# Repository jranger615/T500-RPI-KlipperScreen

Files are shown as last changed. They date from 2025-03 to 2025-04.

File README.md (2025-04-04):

 # T500-RPI-KlipperScreen
Tired of the TouchPad for the t500, here we will build our own
This Klipper screen should work for other klipper machines but may require other conifguration changes and a new mount

mail google

> [!IMPORTANT]
>### RPI5 Version
> * Added RPI5 version of STLs.
> * It however may require different usb/pwr wires/buck converter.
> * Uses official RPI5 FAN

> ### If you wish to tip and help continue my work on mods please use:
>* Paypal: Jeff.b.ranger@gmail.com
>* Venmo: @Jeff-Ranger-1

## Things to BUY
  * Raspberry PI 4B 4GB RAM https://chicagodist.com/products/raspberry-pi-4-model-b-4gb  (I will remodel this for RPi5 as well)
  * SD Card https://chicagodist.com/products/raspberry-pi-official-noobs-microsd-card?variant=40342062268495
  * SD Card Reader (If your Laptop or COmputer Doesnt Have one)
  * 7" Touch Screen https://www.amazon.com/dp/B0B2QW89DR?ref_=ppx_hzsearch_conn_dt_b_fed_asin_title_2
  * 24v > 5V BUCK Power Adapter https://www.amazon.com/dp/B0CRVW7N2J 
  * HDMI Cord https://www.amazon.com/dp/B0CCKXH13W
  * USBA-USBC Cord https://www.amazon.com/dp/B0BRQY1FLG
  * USBA-USB Micro Cord https://www.amazon.com/dp/B0BHNVLW1Z
  * USB-C Extension https://www.amazon.com/dp/B0DKHPS1L3
  * M3 and M4 Heat Inserts
  * **Optional**  Power Supply https://www.amazon.com/dp/B0BMGJNSVS (This just makes it easier to power your Pi and do your configurations not attached to your printer)
  * m3 bolts
  * m4x6 bolts (Attatchment to Printer)
  * Screws https://www.amazon.com/dp/B078ZVQ7XM (Mounts the LCD Screen to case)
  * RPI4 Fan https://www.amazon.com/dp/B091L1XKL6

## Software to Download
  * Raspberry Pi Imager https://www.raspberrypi.com/software/
  * Putty https://www.chiark.greenend.org.uk/~sgtatham/putty/latest.html

## Things to Print
Located: https://github.com/jranger615/T500-RPI-KlipperScreen/tree/main/stl
  * LCD_FRONT.stl
  * RPI4_LCD_BACK.stl
  * RPI4-TOP.stl
  * Vertical-LCD-Mount.stl or Horizon-LCD-Mount.stl
    
 

## Install Mainsail on SD CARD
  * First, take the MicroSD you’ll use for your Raspberry Pi and connect it to your computer. 
  * $Download and install the Pi Imager tool and launch it.
  * Click Choose Device, and select Raspberry PI 4
  * Click “Choose OS”, scroll down to “Other specific-purpose OS”, choose “3D printing”, and then select Mainsail OS.
  * Choose Storage, and make sure to select the SD card.
  * Click Next
  * Click Edit Setting
    
    
  * Set a Host name of your choice
  * set MKS as the user  (***This is important so we dont have to edit many configs on the t500)
    
    
  * Set makerbase as the password
  * Enable and SET your WIFI Settings
  * Click Save
  * Click Yes
  * Click Yes to write to SD Card
  * Once Complete put the SD Card in your Raspberry PI

## Install Kiauh
 * Attach your Raspberry PI to the power cord and turn it on
 * Open Putty.exe and add host name you used in the Mainsial install  EX: mkspiB.local  (May need to attach network cord if wifi doesnt work after a couple minutes)
   
 
 * Click Open
 * Click Accept
  
  

 * Enter user: MKS 
 * Click enter
 * Enter password: makerbase
 * Click Enter
 * Type: sudo apt-get update && sudo apt-get install git -y
 * click enter
 * Enter password: makerbase
 * Click enter
 * type: cd ~ && git clone https://github.com/dw-0/kiauh.git
 * click enter
 * type: ./kiauh/kiauh.sh
 * click enter
 
 
 * type: 1 and click enter
 * type: 1 and click enter to install
 * type 7 and click enter
   
  

 * When Prompted "Press enter for default (Yes) [Y/n]" Click Enter
 * When Prompted "Press enter for default (Xserver) Backend Xserver or Wayland (cage)? x/w" Click Enter  (This will take awhile to complete)
 * When Prompted "Install NetworkMangher for the network panel [Y/n]" Type Y
 * Click enter

 ## Install Kamp 
  If you are not currently using KAMP you can skip this step 

 * Reconnect to putty like above
 * Browse to https://github.com/kyleisah/Klipper-Adaptive-Meshing-Purging and follow the installation commands

## Fix Wifi Configurations (This is only needed if all WIFI options arent showing up)
When you first set up a Raspberry Pi, sometimes you'll need to manually set the timezone/location to allow you to make a WiFi connection (even though the initial setup screens appear to set this for you). 
* Putty into your device
* type: sudo raspi-config
  
 
* Select Localization Options again and Selec WLAN Country
* Set TimeZone
* Select Localization Options again and Selec WLAN Country
* Press the Right Direction button and Click Finish
* type: Sudo reboot
* Click Enter
May Also Require Disabling Network Manager and Re-Enabling it in Advanced Options

## Horizonal Orientation Configs
 * Putty into device as before
 * type: sudo nano /boot/config.txt
 * Add the below...Some can be uncommented in other sections but you can add this to the bottom.
  ```ruby
framebuffer_width=1024
framebuffer_height=600
hdmi_force_hotplug=1
hdmi_cvt=1024 600 60 3 0 0 0
hdmi_group=2
hdmi_mode=87
 ```
* Ctrl+X to save
* Type Y to save
  
## For Vertical orientation ONLY 
 Note: This orientation appears a bit stretched to me
 * Putty into device as before
 * type: sudo nano /boot/config.txt
 * find "dtoverlay=vc4-fkms-v3d" and comment it out by putting a # in front of it (This is RPI4 SPecific)
 * Goto the end of the file 
 * add: display_rotate=3
 * Ctrl-X to exit
 * Y to Save
 * type: cd /usr/share/X11/xorg.conf.d/
 * type: sudo nano 40-libinput.conf
 * find one that has a section that has "Identifier ... touchscreen catchall".
 * Add: Option "TransformationMatrix" "0 -1 1 1 0 0 0 0 1"
 * Ctrl-X to exit
 * Y to Save

## Backup Klipper Configs
 * Open your browser and goto your current IP or name for your t500
 * Click the Machine Tab on the Left
 * Click the Check box for your config files and then click download (More files may apply depending on your configuration)
 * Stock Files:
  ```ruby
   printer.cfg
   plr.cfg
   moonracker.cfg
   fluidd.cfg
  ```
 * They will be download as a zip so you will have to extract them before uploading them later 

## Update Klipper
 * open your browser and goto your host name EX: mkspiB.local
 * Click the machine tab in Klipper
 * On the right side File Manager, Click Update on all the sections. (I prefer to do one at a time over the Update All Function at the bottom)
  
 * This may disconnect and require you to refresh your browser to get back in
 * Click the upload button in the config files section and upload all your files you backedup from Klipper
   
   
 * open printer.cfg
 * comment out the following:
```ruby
#[mcu rpi]
#serial: /tmp/klipper_host_mcu

#[adxl345]
#cs_pin: rpi:None
#spi_bus: spidev0.0

#[resonance_tester]
#accel_chip: adxl345
#probe_points:230, 230, 20  # an example
#accel_per_hz:50
#min_freq:1
##max_smoothing:0.2
#hz_per_sec:0.5
```
* Commet out max_accel_to decel replace
```ruby
#max_accel_to_decel: 1500 
minimum_cruise_ratio: .5
```

## Assemble the LCD Device
 * Add 4 - M3x4 Heater inserts into the LCD Case

  
 * Insert the LCD into the Front Case and Attach the 4 small screws in each corner to hold in firmly in place
 * Add 6 - M3x4 Heater inserts into the RPI4 LCD Case Back. 

  
 * Take your RPI4 and insert it to the RPI4 TOP.
 * Install RPI4 Fan per instructions included
 * Place the TOP on the LCD Backing plateon RPI4
 * Insert 4 m3x12 bolts in the 4 corners to hold them in place
 * Attach the back to the LCD front and install 4-m3x6 bolts to attach all together
 * Install 3 - m4x6 into the Mounting Bracket
 * Install the mounting bracket onto the backing plate using 4 - m3x6 bolts
 * Attach all the wires from the RPI4 to the LCD
 * HDMI to HDMI Micro
 * USB-A to USB-C (Closest to the HDMI enabled the touch screen)
 * Make sure the on switch is on, this is easy to see through the large hole in the mesh backing

## Remove Touch PAD
 * Remove the Power Cord from the Tablet
 * Remove the USB Cord from the Tablet
 * Remove the 3 Allen Screws from the back of the Touch Pad
 * Push the bed to the back
 * Remove the 4 Screws from the t500 Cover
 * Pull the bed forward
 * Remove the back 3 screws
 * Push the bed back again
 * Pull the cover off the t500
 * Remove the USB and Power Cord

   
 * Cut the zip tie holding the wires in place and remove the wires from your t500 
 * Cut the END off the Power Cord and Solder the wires to your Buck Connector.
 * Plug the Buck Connector into the board and run the wires to out towards the LCD Mount (You may want to use self tap screws or double sided tape to mount the buck connector)
 * Attach the USB-C Extension to the power cord
 * Run the USB-C wire to USB-A wire from the board out towards the Touch PAD

## Attach new RPI Touch screen
 * Attach the New LCD to the Mounting bracket using 3 - m4-6 screws
 * Attach the USB C power cord
 * Attach the USB C to USB A to the PI
 * Power on printer and make sure everything attaches
 * Re-Install the t500 top plate with the 6 screws
 * ENJOY

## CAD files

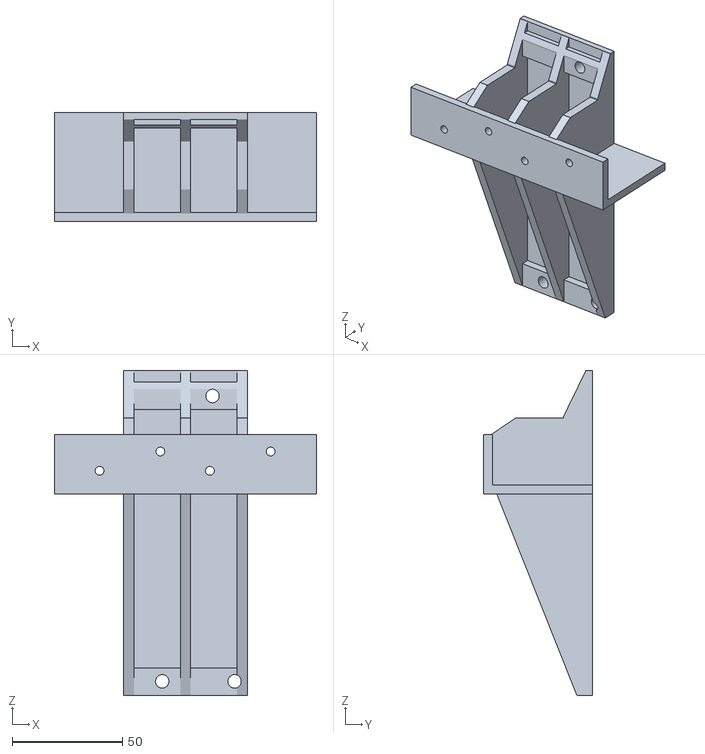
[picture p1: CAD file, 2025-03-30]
stl/Horizon-LCD-Mount.stl
119.0 x 49.3 x 147.3

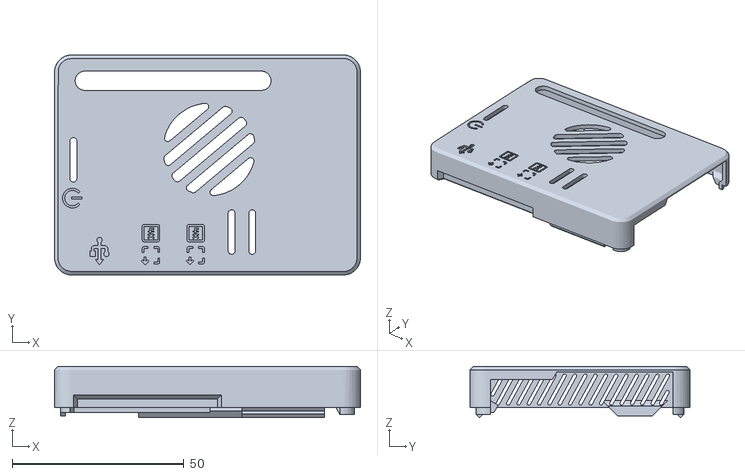
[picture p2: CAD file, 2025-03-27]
stl/RPI5-TOP.stl
89.0 x 64.0 x 14.9

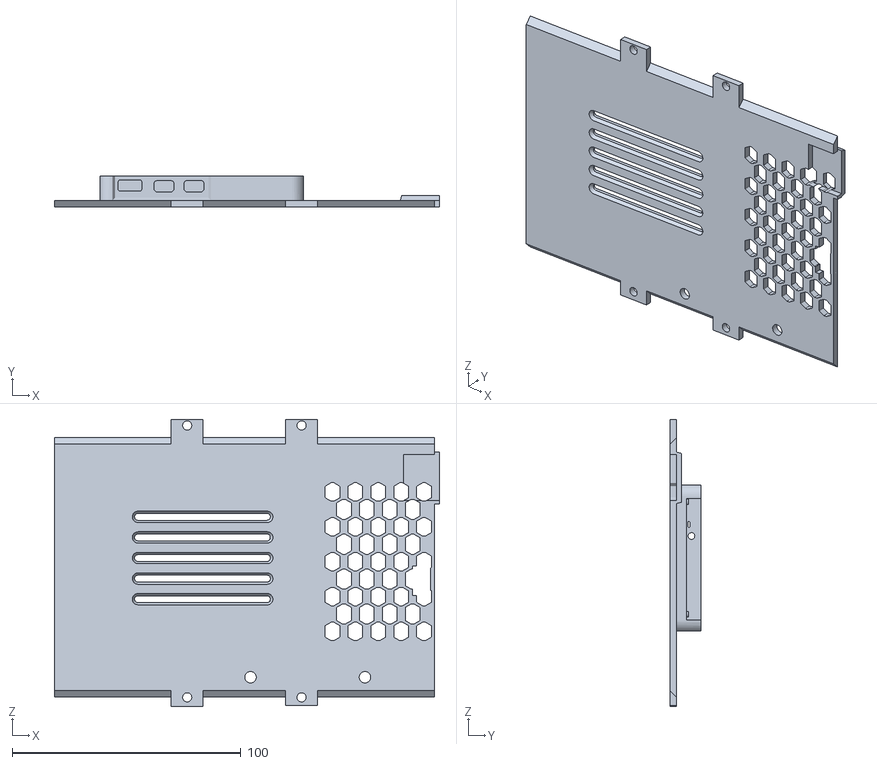
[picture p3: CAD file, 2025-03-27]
stl/RPI5_LCD_BACK.stl
168.3 x 13.4 x 125.6

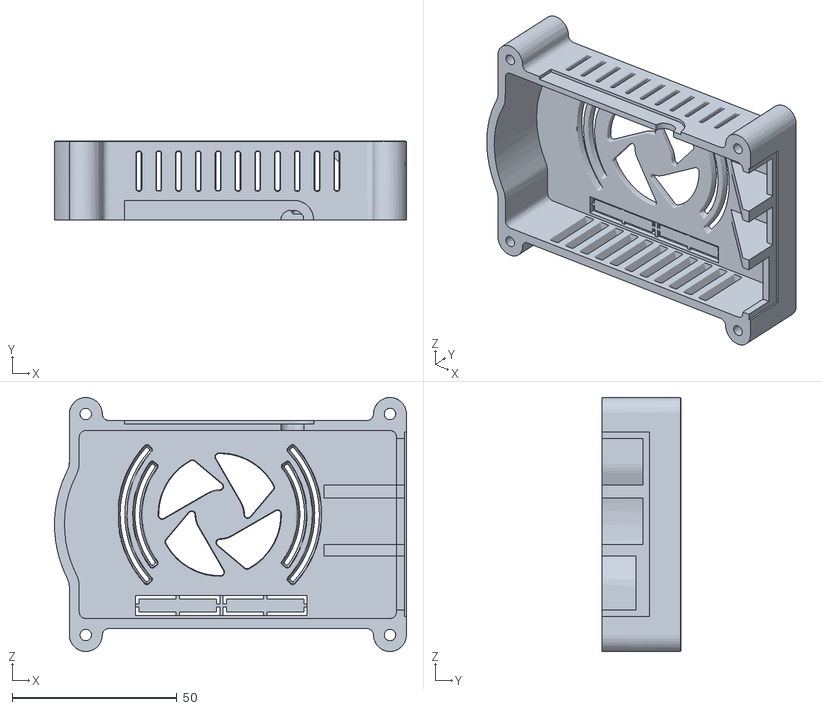
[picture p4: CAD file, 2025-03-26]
stl/RPI4-TOP.stl
106.7 x 24.0 x 77.0

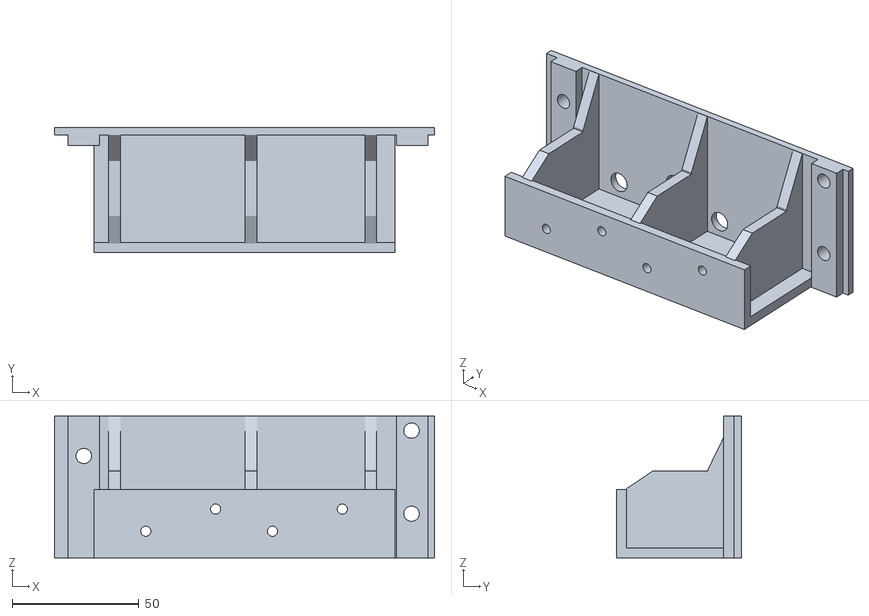
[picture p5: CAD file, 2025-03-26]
stl/Vertical-LCD-Mount.stl
150.0 x 49.3 x 56.0

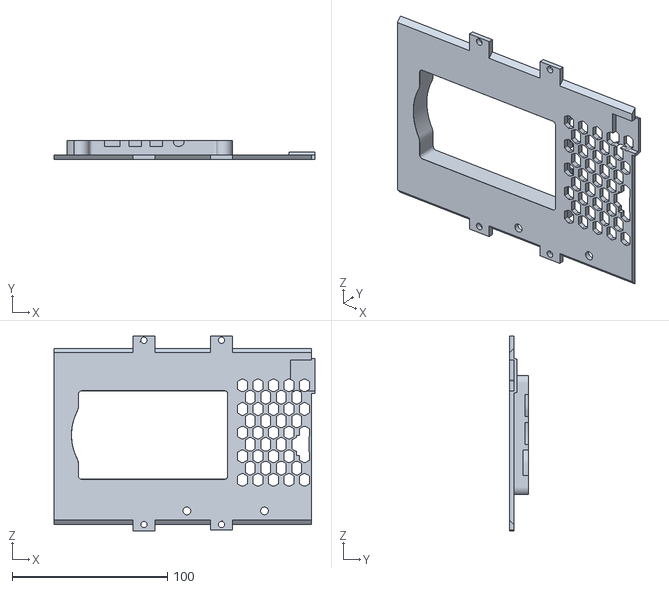
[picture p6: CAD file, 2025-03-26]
stl/RPI4_LCD_BACK.stl
168.3 x 12.3 x 125.6

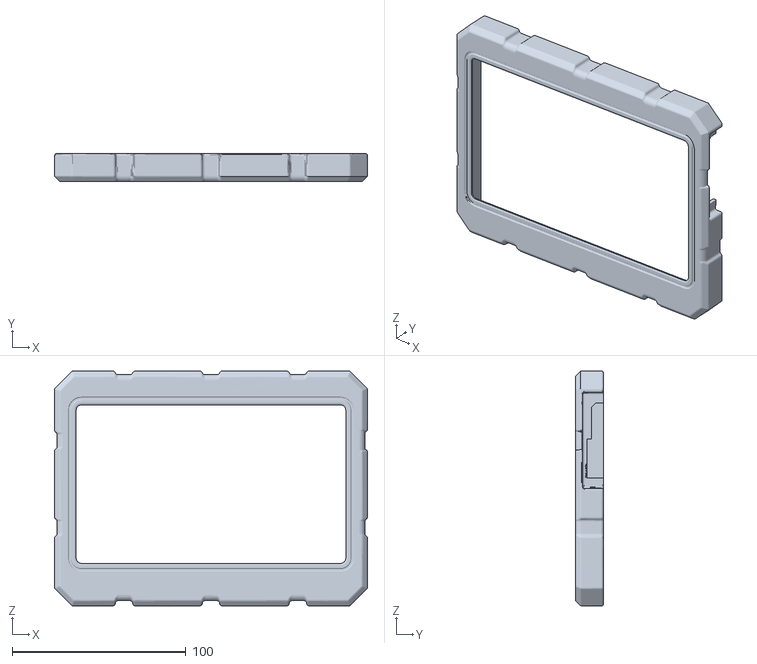
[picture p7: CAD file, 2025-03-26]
stl/LCD_FRONT.stl
180.0 x 16.3 x 135.0
